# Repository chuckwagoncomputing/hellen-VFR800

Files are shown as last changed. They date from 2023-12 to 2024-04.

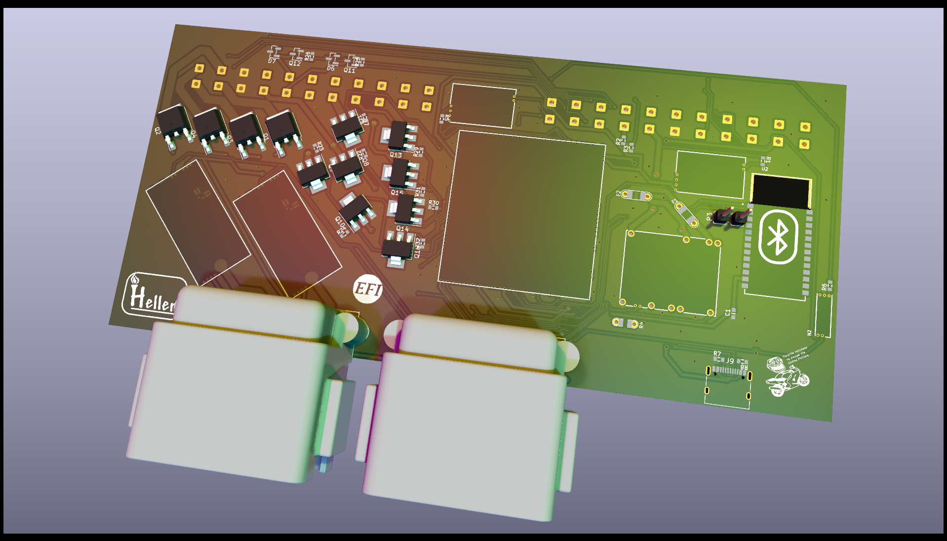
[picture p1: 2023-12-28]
uaeficopiedtovfr.png

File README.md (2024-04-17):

bumpThis repo contains files to build a standalone plug and play RusEFI Hellen based ECU for a 99 Honda VFR800. The prototype is unfinished and currently none of these files can be used to make a functioning ECU

A quick look at the wiring diagrams suggest this hardware should also be compatible with the CBR600F4i, CBR929RR, and 01-03 CBR1100xx  if the ECU connectors were repinned.

In addition to the above it may be able to replace the ignition module/ECU of a 98-08 VT1100C, 01-07 VT750DC, 02-04 VTX1800, RC51, and 2003-09 VTX1300 with some harness repinning

Features in progress as of v0.03:

Drop in ECU replacement for 99-01 VFR800 with addition of 2 wideband oxygen sensors

4x sequential ignition/injection

CANBUS

2x Wideband oxygen sensor channels

3x lowside driver output on rear connector

Inputs for analog sensor on rear connector

USB support

Bluetooth connectivity

MicroSD card for logging

VSS input to ECU for eventual implementation of traction control

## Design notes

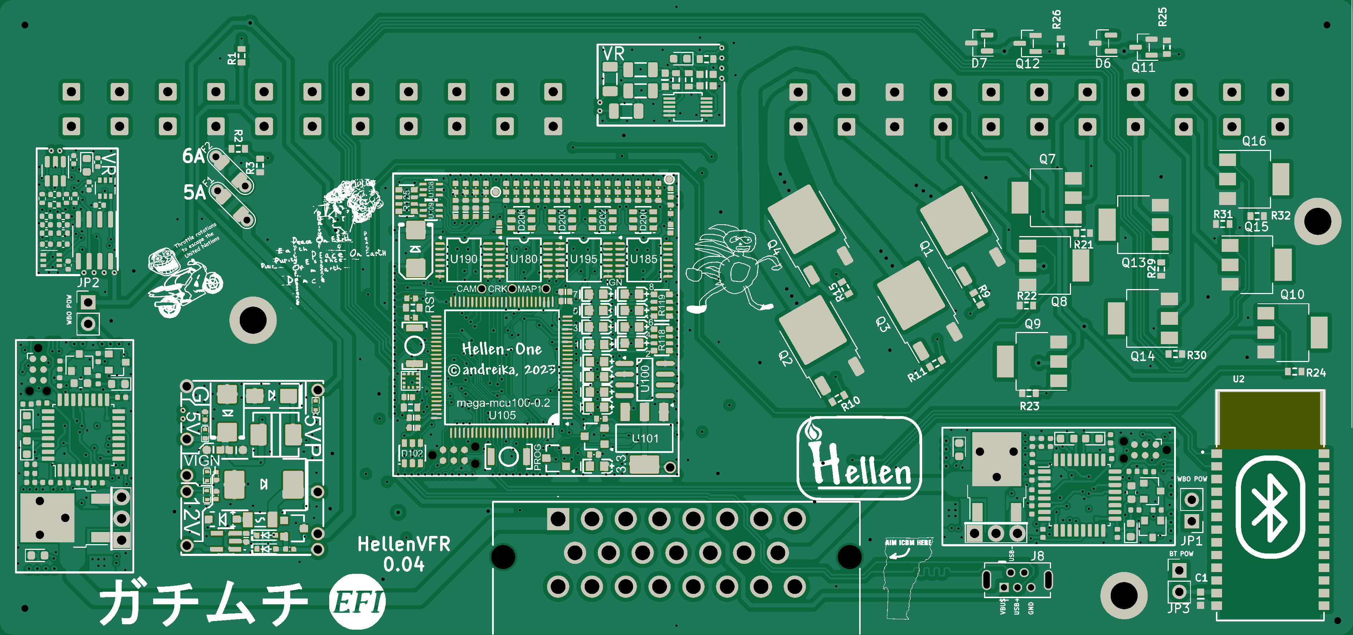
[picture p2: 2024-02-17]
boards/uaeficopiedtovfr-0.04/board/misc/uaeficopiedtovfr-0.04-top.png

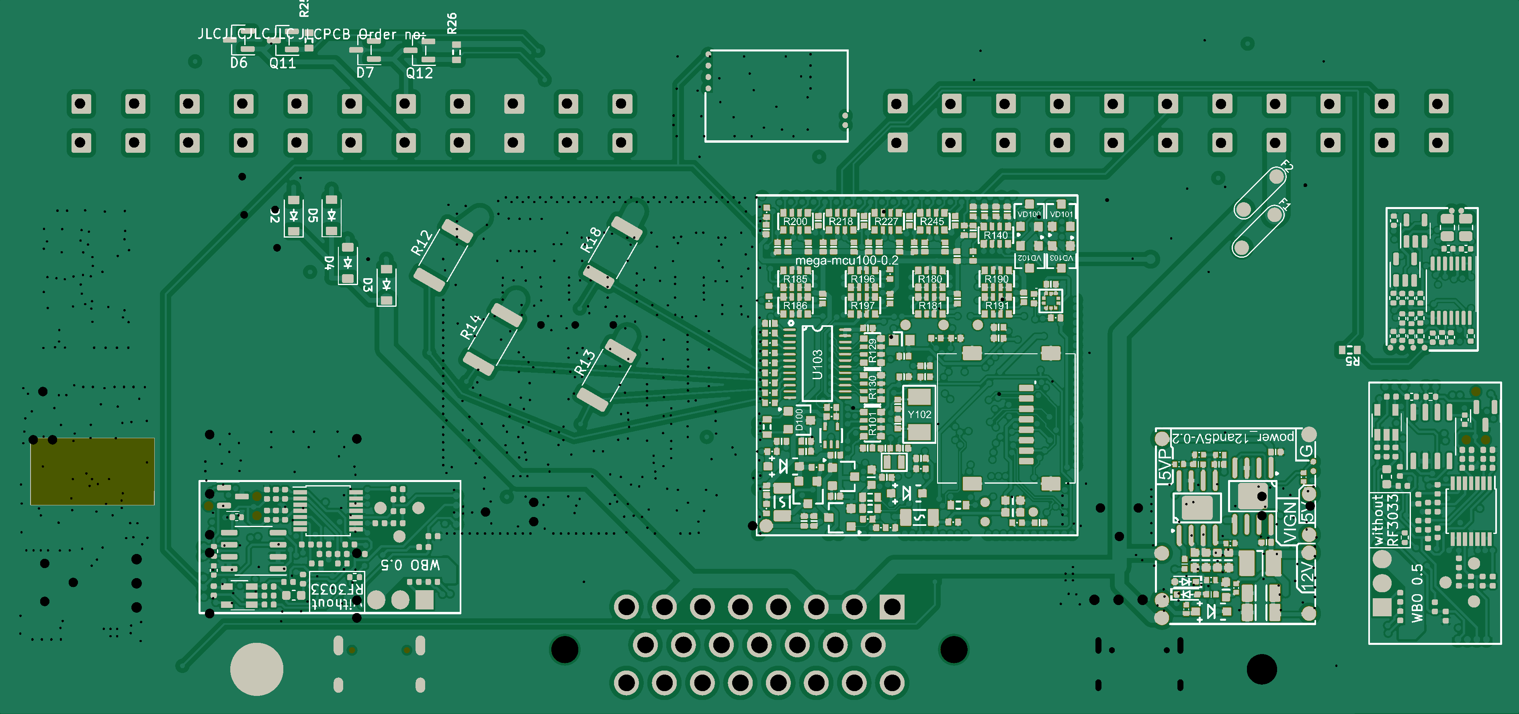
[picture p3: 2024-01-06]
boards/uaeficopiedtovfr-0.03/board/misc/uaeficopiedtovfr-0.03-bottom.png

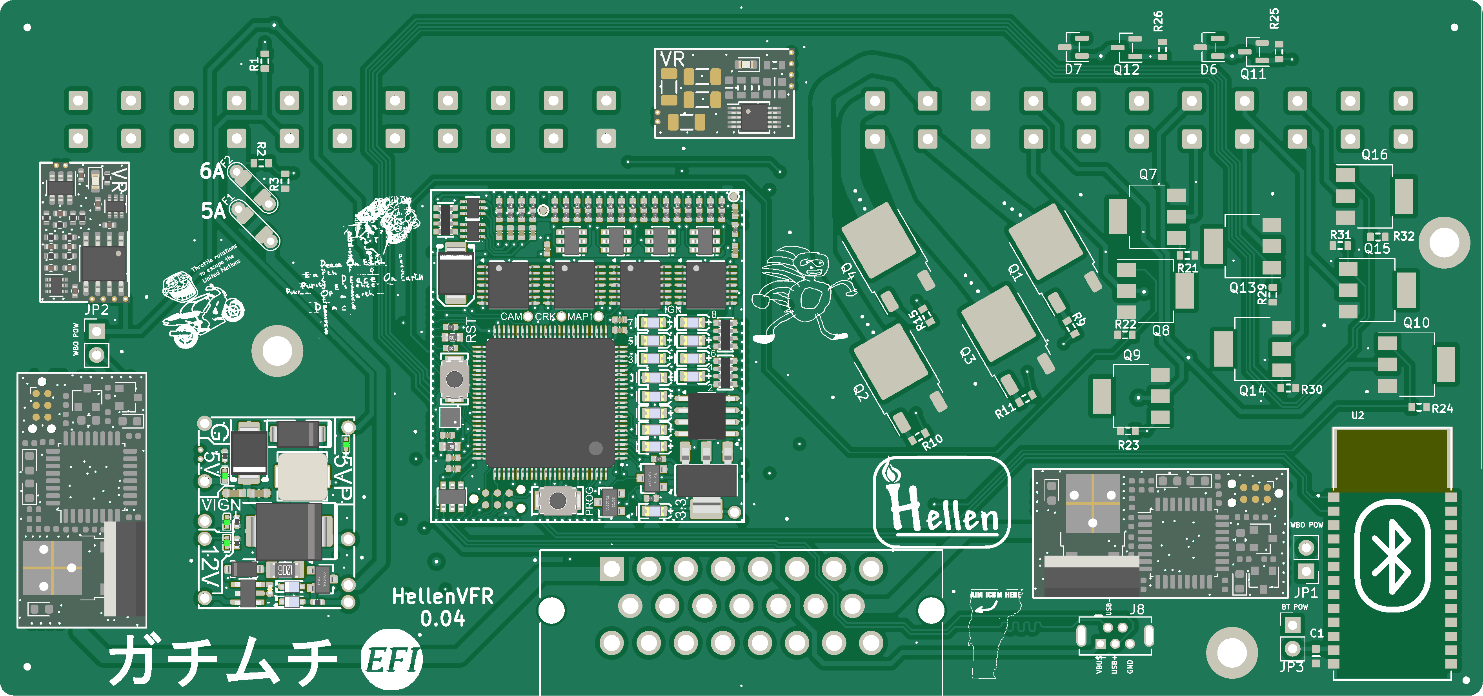
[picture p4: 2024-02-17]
boards/uaeficopiedtovfr-0.04/board/uaeficopiedtovfr-0.04.png

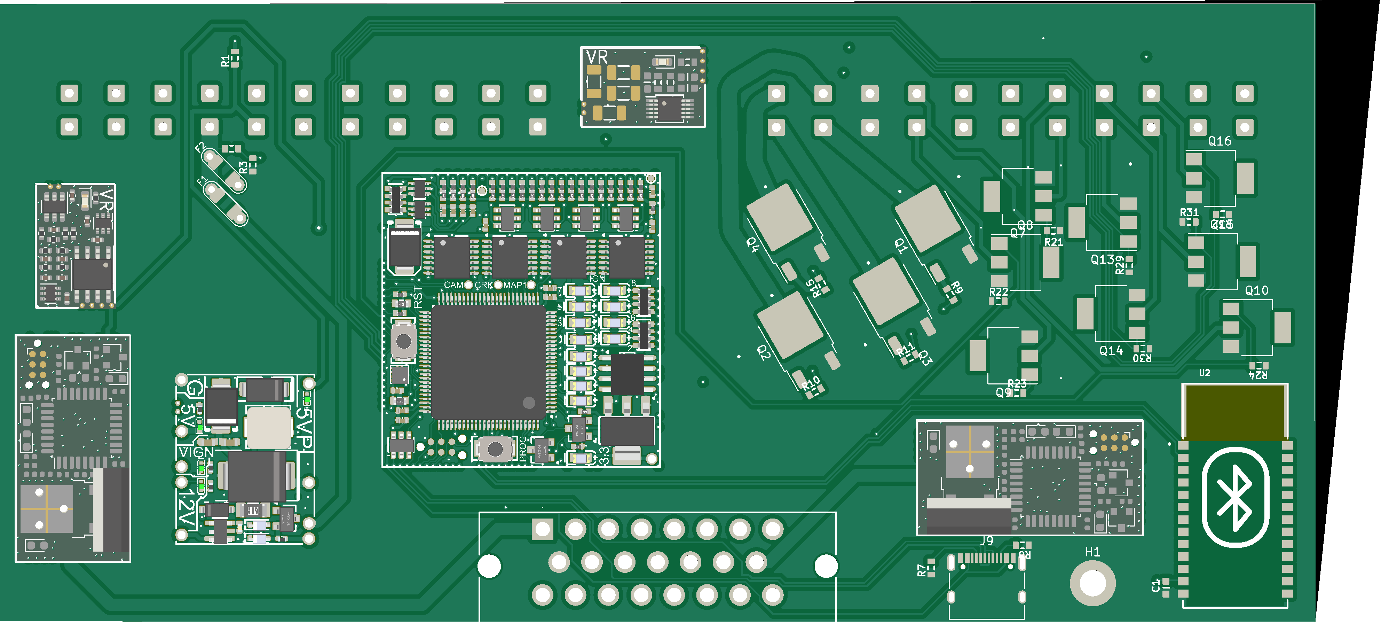
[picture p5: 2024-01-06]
boards/uaeficopiedtovfr-0.03/board/uaeficopiedtovfr-0.03.png

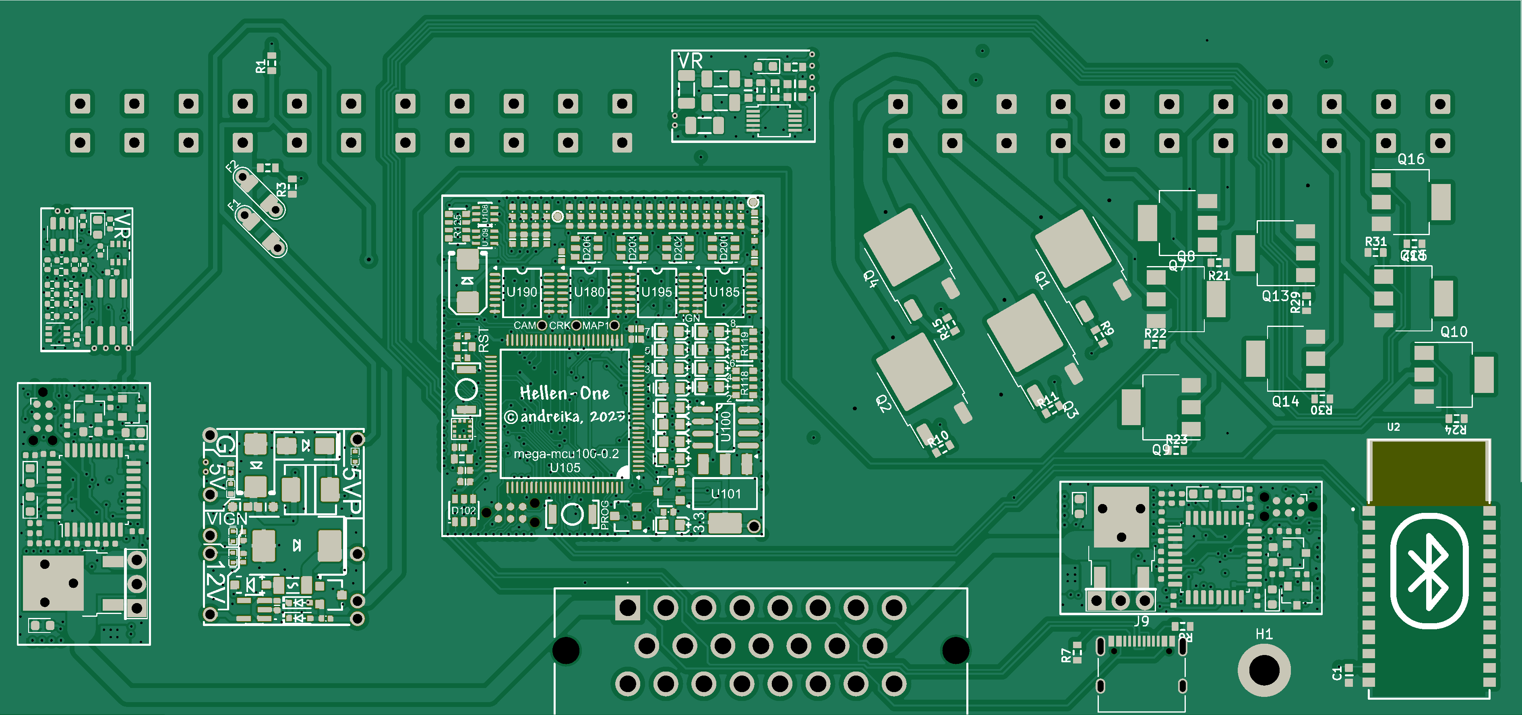
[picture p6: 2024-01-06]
boards/uaeficopiedtovfr-0.03/board/misc/uaeficopiedtovfr-0.03-top.png

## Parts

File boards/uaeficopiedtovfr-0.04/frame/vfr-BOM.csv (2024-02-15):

Comment | Designator | Footprint | LCSC Part #
100n | C1 | C0603 | C14663
B5819W | D2 | SOD-123 | C8598
B5819W | D3 | SOD-123 | C8598
B5819W | D4 | SOD-123 | C8598
B5819W | D5 | SOD-123 | C8598
PSM712-LF | D6 | SOT-23 | C32677
PSM712-LF | D7 | SOT-23 | C32677
12H1500D | F1 | PAD-1206-PAD | C182446
12H1500D | F2 | PAD-1206-PAD | C182446
RUSEFI_LOGO | G3 | rusefi_logo
LOGO | G4 | LOGO
MountingHole_Pad | H1 | MountingHole_3.2mm_M3_DIN965_Pad
MountingHole_Pad | H2 | MountingHole_3.2mm_M3_DIN965_Pad
Conn_01x06 | J3 | PinHeader_1x06_P2.54mm_Vertical | C37208
1-776087-1 | J4 | 17760871
Conn_01x06 | J6 | PinHeader_1x06_P2.54mm_Vertical | C37208
MUSBD111M0 | J7 | CONN4_BD111M0_AMP
USB_B_Mini | J8 | USB-MINI-B-VERTICAL
USB_C_Receptacle_USB2.0 | J9 | USB_C_Receptacle_XKB_U262-16XN-4BVC11 | C2927038
Jumper_2_Bridged | JP1 | PinHeader_1x02_P2.54mm_Vertical
Jumper_2_Bridged | JP2 | PinHeader_1x02_P2.54mm_Vertical
Jumper_2_Bridged | JP3 | PinHeader_1x02_P2.54mm_Vertical
Module:power_12and5V/0.2 | M1 | power_12and5V
Module:knock/0.2 | M2 | knock
Module:vr-discrete/0.4 | M3 | vr-discrete
Module:vr-max9924/0.1 | M4 | vr-max9924
Module:wbo/0.5 | M5 | wbo
Module:mega-mcu100/0.2 | M6 | mega-mcu100
Module:wbo/0.5 | M7 | wbo
Pad | P1 | PAD-TH
Pad | P2 | PAD-TH
Pad | P3 | PAD-TH
Pad | P4 | PAD-TH
ISL9V3040D3S | Q1 | DPAK
ISL9V3040D3S | Q2 | DPAK
ISL9V3040D3S | Q3 | DPAK
ISL9V3040D3S | Q4 | DPAK
ZXMS6005SGTA | Q7 | SOT-223 | C174042
ZXMS6005SGTA | Q8 | SOT-223 | C174042
ZXMS6005SGTA | Q9 | SOT-223 | C174042
ZXMS6005SGTA | Q10 | SOT-223 | C174042
AO3400A | Q11 | SOT-23 | C20917
AO3400A | Q12 | SOT-23 | C20917
ZXMS6005SGTA | Q13 | SOT-223 | C174042
ZXMS6005SGTA | Q14 | SOT-223 | C174042
ZXMS6005SGTA | Q15 | SOT-223 | C174042
ZXMS6005SGTA | Q16 | SOT-223 | C174042
4.7k | R1 | R0603
33k | R2 | R0603 | C4216
6.8k | R3 | R0603 | C23212
Jumper-Pad-Pad | R4 | PAD-0805-PAD | C17477
0 | R5 | R0603
0 | R6 | R0603 | C21189
5.6k | R7 | R0603 | C23189
5.6k | R8 | R0603 | C23189
22 | R9 | R0603 | C23345
22 | R10 | R0603 | C23345
22 | R11 | R0603 | C23345
0 | R12 | R2512 | C25469
0 | R13 | R2512 | C25469
0 | R14 | R2512 | C25469
22 | R15 | R0603 | C23345
0 | R18 | R2512 | C25469
4.7k | R21 | R0603 | C23162
4.7k | R22 | R0603 | C23162
4.7k | R23 | R0603 | C23162
4.7k | R24 | R0603 | C23162
4.7k | R25 | R0603 | C23162
4.7k | R26 | R0603 | C23162
4.7k | R29 | R0603 | C23162
4.7k | R30 | R0603 | C23162
4.7k | R31 | R0603 | C23162
4.7k | R32 | R0603 | C23162
~ | text1 | trollfaceVFR
~ | U1 | VFRboardempty
JDY-33 | U2 | JDY-33

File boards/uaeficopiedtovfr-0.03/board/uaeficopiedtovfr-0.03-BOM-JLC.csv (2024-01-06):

Comment | Designator | Footprint | LCSC Part #
100n | C1, C772 | C0603 | C14663
B5819W | D2, D3, D4, D5, D416, D417, D101, D107 | SOD-123 | C8598
PSM712-LF | D6, D7, D411 | SOT-23 | C32677
12H1500D | F1, F2 | PAD-1206-PAD | C182446
Conn_01x06 | J3, J6 | PinHeader_1x06_P2.54mm_Vertical | C37208
USB_C_Receptacle_USB2.0 | J9 | USB_C_Receptacle_XKB_U262-16XN-4BVC11 | C2927038
ZXMS6005SGTA | Q7, Q8, Q9, Q10, Q13, Q14, Q15, Q16 | SOT-223 | C174042
AO3400A | Q11, Q12, Q101, Q103 | SOT-23 | C20917
33k | R2, R120 | R0603 | C4216
6.8k | R3 | R0603 | C23212
Jumper-Pad-Pad | R4 | PAD-0805-PAD | C17477
0 | R6 | R0603 | C21189
5.6k | R7, R8 | R0603 | C23189
22 | R9, R10, R11, R15 | R0603 | C23345
0 | R12, R13, R14, R18 | R2512 | C25469
4.7k | R21, R22, R23, R24, R25, R26, R29, R30, R31, R32 | R0603 | C23162
47u | C410, C412 | C1206 | C96123
100n | C411, C413, C420 | C0402 | C307331
1u | C414, C415, C755, C758, C761, C762, C763, C765, C766, C767, C600, C607, C609, C610, C611, C600_2, C607_2, C609_2, C610_2, C611_2 | C0402 | C52923
10u | C421, C422, C423, C424, C425, C426 | C0603 | C96446
4.7u | C427, C616, C616_2 | C0603 | C19666
10n | C428, C756, C757, C760, C764, C768, C769, C202, C208, C209, C210, C211, C212, C213, C214, C215 | C0402 | C15195
220p | C429 | C0402 | C1530
1N4148WS | D410, D412, D413, D414 | SOD-323 | C2128
SMCJ30A | D418 | SMC | C310046
SS34 | D420 | SMA | C8678
P6SMB6.8CA | D421, D205 | SMB | C78395
SMD1206P050TF/24 | F410 | SMD1206 | C209741
2.2uH | L420 | L1210 | C36828
MWSA0503-10uH | L421 | MWSA0503 | C139506
MHT136UGCT | LED1, LED2, LED3, LED4 | LED0402 | C434447
6.8k | R410, R413 | R0402 | C25917
33k | R411, R424, R425 | R0402 | C25779
1 | R420 | R0402 | C25086
10k | R421, R426, R427, R757, R762, R763, R767, R768, R604, R605, R613, R614, R618, R619, R625, R102, R103, R105, R107, R108, R109, R121, R124, R126, R127, R128, R132, R135, R136, R137, R138, R139, R141, R142, R228, R229, R230, R231, R232, R233, R234, R235, R246, R247, R248, R249, R250, R251, R252, R253, R604_2, R605_2, R613_2, R614_2, R618_2, R619_2, R625_2 | R0402 | C25744
68k | R422, R760, R602, R603, R602_2, R603_2 | R0402 | C36871
12k | R423, R754 | R0402 | C25752
4.7k | R428, R144, R203, R204, R207, R208, R219, R220, R223, R224 | R0402 | C25900
MIC5205-3.3YM5 | U410 | SOT23-5 | C37970
TLS115 | U411 | PG-DSO-8 EP | C540242
LMR14020 | U420 | SOP8 | C187824
1n | C751, C135, C139, C141, C142, C143, C144, C145, C146, C200, C201, C203, C225, C226, C227, C228 | C0402 | C1523
470n | C752 | C0402 | C47339
100n | C753, C754, C759, C601, C602, C605, C608, C612, C613, C614, C615, C617, C618, C100, C101, C105, C108, C111, C112, C113, C119, C120, C122, C124, C126, C127, C130, C134, C147, C180, C185, C190, C195, C220, C221, C222, C601_2, C602_2, C605_2, C608_2, C612_2, C613_2, C614_2, C615_2, C617_2, C618_2 | C0402 | C1525
LED-GREEN-0603 | D751, D771, D601, D104, D108, D601_2 | LED-0603 | C72043
2.2k | R751, R122, R123, R146, R147 | R0402 | C25879
10k | R752, R753 | R0805 | C17414
100k | R755, R756, R758, R759, R615, R621, R615_2, R621_2 | R0402 | C25741
10 | R761, R764, R769, R606, R110, R111, R112, R113, R114, R115, R116, R117, R606_2 | R0402 | C25077
1k | R765, R766, R600, R601, R616, R617, R622, R626, R627, R628, R600_2, R601_2, R616_2, R617_2, R622_2, R626_2, R627_2, R628_2 | R0402 | C11702
SRV05-4-P-T7 | U751, D102, D200, D202, D203, D206 | SOT23-6 | C85364
74AHC1G02 | U752, U757 | SOT23-5 | C7463
MCP6004 | U753, U600, U180, U185, U190, U195, U600_2 | TSSOP14 | C50282
MAX9142 | U754 | SO8 | C18567
NC7SB3157P6X | U755, U756 | SOT-363 | C87403
1n | C771 | C0603 | C1588
22u | C773, C117, C123 | C0603 | C59461
4.7k | R771, R772, R773, R774 | R1206 | C17936
10k | R776, R777 | R0603 | C25804
MAX9924UAUB+ | U771 | MSOP-10_3x3mm_P0.5mm | C143633
33n | C603, C603_2 | C0402 | C1585
LED-RED-0603 | D600, D603, D103, D600_2, D603_2 | LED-0603 | C2286
LED-BLUE-0603 | D602, D105, D109, D110, D111, D112, D113, D114, D115, D116, D602_2 | LED-0603 | C72041
PESD1CAN | D604, D100, D604_2 | SOT-23 | C343993
VND7NV04TR-E | Q600, Q600_2 | DPAK | C155605
22k | R607, R607_2 | R0402 | C25768
47 | R608, R608_2 | R0402 | C25118
61.9 | R609, R609_2 | R0603 | C23092
20k | R610, R611, R612, R610_2, R611_2, R612_2 | R0402 | C25765
27k | R620, R623, R620_2, R623_2 | R0402 | C25771
3.3k | R624, R624_2 | R0402 | C25890
AD8628 | U601, U601_2 | TSOT23-5 | C29309
STM32F042K6Tx | U602, U602_2 | LQFP32 | C69216
REF3033 | U603, U102, U603_2 | SOT-23 | C36658
XC6206P332MR | U604, U604_2 | SOT-23 | C5446
TJA1051T/3/1J | U605, U100, U605_2 | SO-8_3.9x4.9mm_P1.27mm | C38695
STM32F429VGT6 | U105 | LQFP100 | C95448
SN74LVC4245APWR | U103 | TSSOP24 | C7859
SN74LVC1G06DCKR | U110 | SOT-353 | C7828
SMD1206B035TF/16 | F100, F101 | R1206 | C269114
Molex MicroSD 47219-2001 | J100 | SDAMB-012 | C164170
LPS22HBTR | U107 | HLGA-10L | C94049
LIS2DH12TR | U106 | LGA12 | C110926
LED-YELLOW-0603 | D106 | LED-0603 | C72038
LDL1117S33R | U101 | SOT-223 | C435835
BTN | S100, S101 | SMD-2_2.9x3.9x1.7 | C115357
BLM18AG601SN1D | L100 | L0603 | C19330
BAT54S | VD100, VD101, VD102, VD103 | SOT-23 | C47546
AO3401A | Q100, Q102 | SOT-23 | C15127
680k | R201, R202, R205, R206, R221, R222, R225, R226 | R0402 | C163456
510 | R133, R134 | R0603 | C23193
510 | R254, R255, R256, R258 | R0402 | C25123
470 | R101, R118, R119 | R0603-4 | C25510
120 | R100 | R0603 | C22787
100 | R104, R106 | R0603 | C22775
74LVC2G17GW,125 | U108, U109 | SOT-363 | C80500
32.768 kHz | Y101 | SMD2012 | C99009
20 MHz | Y102 | SMD5032 | C112566
18p | C132, C136 | C0402 | C1549
12p | C115, C116 | C0402 | C1547
10k | R129, R130, R140 | R0603-4 | C29718
5.1k | R195 | R0402 | C25905
4.7u | C102, C103, C104, C106, C107, C137, C138, C140 | C0402 | C23733
4.7k | R125, R180, R181, R185, R186, R190, R191, R196, R197, R200, R218, R227, R245 | R0603-4 | C66697
2.2u | C114, C131, C223, C224, C229 | C0402 | C12530
1u | C133 | C0603 | C519560
0 | R131, R143, R145, R148 | R0402 | C17168
nSMD050-24V | F42333310 | SMD1206 | C70076

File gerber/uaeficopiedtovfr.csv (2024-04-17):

Comment | Designator | Footprint | LCSC Part #
100n | C1 | hellen-one-common:C0603 | C14663
B5819W | D2 | hellen-one-common:SOD-123 | C8598
B5819W | D3 | hellen-one-common:SOD-123 | C8598
B5819W | D4 | hellen-one-common:SOD-123 | C8598
B5819W | D5 | hellen-one-common:SOD-123 | C8598
PSM712-LF | D6 | hellen-one-common:SOT-23 | C32677
PSM712-LF | D7 | hellen-one-common:SOT-23 | C32677
12H1500D | F1 | hellen-one-common:PAD-1206-PAD | C182446
12H1500D | F2 | hellen-one-common:PAD-1206-PAD | C182446
RUSEFI_LOGO | G3 | kicad6-libraries:rusefi_logo
LOGO | G4 | hellen-one-common:LOGO
MountingHole_Pad | H1 | MountingHole:MountingHole_3.2mm_M3_DIN965_Pad
MountingHole_Pad | H2 | MountingHole:MountingHole_3.2mm_M3_DIN965_Pad
Conn_01x06 | J3 | Connector_PinHeader_2.54mm:PinHeader_1x06_P2.54mm_Vertical | C37208
1-776087-1 | J4 | 17760871
Conn_01x06 | J6 | Connector_PinHeader_2.54mm:PinHeader_1x06_P2.54mm_Vertical | C37208
MUSBD111M0 | J7 | usbb:CONN4_BD111M0_AMP
USB_B_Mini | J8 | hellen-one-common:USB-MINI-B-VERTICAL
USB_C_Receptacle_USB2.0 | J9 | Connector_USB:USB_C_Receptacle_XKB_U262-16XN-4BVC11 | C2927038
Jumper_2_Bridged | JP1 | Connector_PinHeader_2.54mm:PinHeader_1x02_P2.54mm_Vertical
Jumper_2_Bridged | JP2 | Connector_PinHeader_2.54mm:PinHeader_1x02_P2.54mm_Vertical
Jumper_2_Bridged | JP3 | Connector_PinHeader_2.54mm:PinHeader_1x02_P2.54mm_Vertical
Module-power_12and5V-0.2 | M1 | hellen-one-power_12and5V-0.2:power_12and5V
Module-knock-0.2 | M2 | hellen-one-knock-0.2:knock
Module-vr-discrete-0.4 | M3 | hellen-one-vr-discrete-0.4:vr-discrete
Module-vr-max9924-0.1 | M4 | hellen-one-vr-max9924-0.1:vr-max9924
Module-wbo-0.5 | M5 | hellen-one-wbo-0.5:wbo
Module:mega-mcu100/0.2 | M6 | hellen-one-mega-mcu100-0.2:mega-mcu100
Module-wbo-0.5 | M7 | hellen-one-wbo-0.5:wbo
Pad | P1 | hellen-one-common:PAD-TH
Pad | P2 | hellen-one-common:PAD-TH
Pad | P3 | hellen-one-common:PAD-TH
Pad | P4 | hellen-one-common:PAD-TH
ISL9V3040D3S | Q1 | Package_TO_SOT_SMD:TO-252-2
ISL9V3040D3S | Q2 | Package_TO_SOT_SMD:TO-252-2
ISL9V3040D3S | Q3 | Package_TO_SOT_SMD:TO-252-2
ISL9V3040D3S | Q4 | Package_TO_SOT_SMD:TO-252-2
ZXMS6005SGTA | Q7 | Package_TO_SOT_SMD:SOT-223 | C174042
ZXMS6005SGTA | Q8 | Package_TO_SOT_SMD:SOT-223 | C174042
ZXMS6005SGTA | Q9 | Package_TO_SOT_SMD:SOT-223 | C174042
ZXMS6005SGTA | Q10 | Package_TO_SOT_SMD:SOT-223 | C174042
AO3400A | Q11 | hellen-one-common:SOT-23 | C20917
AO3400A | Q12 | hellen-one-common:SOT-23 | C20917
ZXMS6005SGTA | Q13 | Package_TO_SOT_SMD:SOT-223 | C174042
ZXMS6005SGTA | Q14 | Package_TO_SOT_SMD:SOT-223 | C174042
ZXMS6005SGTA | Q15 | Package_TO_SOT_SMD:SOT-223 | C174042
ZXMS6005SGTA | Q16 | Package_TO_SOT_SMD:SOT-223 | C174042
4.7k | R1 | hellen-one-common:R0603
33k | R2 | hellen-one-common:R0603 | C4216
6.8k | R3 | hellen-one-common:R0603 | C23212
Jumper-Pad-Pad | R4 | hellen-one-common:PAD-0805-PAD | C17477
0 | R5 | hellen-one-common:R0603
0 | R6 | hellen-one-common:R0603 | C21189
5.6k | R7 | hellen-one-common:R0603 | C23189
5.6k | R8 | hellen-one-common:R0603 | C23189
22 | R9 | hellen-one-common:R0603 | C23345
22 | R10 | hellen-one-common:R0603 | C23345
22 | R11 | hellen-one-common:R0603 | C23345
0 | R12 | Resistor_SMD:R_2512_6332Metric | C25469
0 | R13 | Resistor_SMD:R_2512_6332Metric | C25469
0 | R14 | Resistor_SMD:R_2512_6332Metric | C25469
22 | R15 | hellen-one-common:R0603 | C23345
470k | R16 | hellen-one-common:R0603 | C23162
0 | R18 | Resistor_SMD:R_2512_6332Metric | C25469
4.7k | R21 | hellen-one-common:R0603 | C23162
4.7k | R22 | hellen-one-common:R0603 | C23162
4.7k | R23 | hellen-one-common:R0603 | C23162
4.7k | R24 | hellen-one-common:R0603 | C23162
4.7k | R25 | hellen-one-common:R0603 | C23162
4.7k | R26 | hellen-one-common:R0603 | C23162
4.7k | R29 | hellen-one-common:R0603 | C23162
4.7k | R30 | hellen-one-common:R0603 | C23162
4.7k | R31 | hellen-one-common:R0603 | C23162
4.7k | R32 | hellen-one-common:R0603 | C23162
~ | text1 | Customparts:trollfaceVFR
~ | U1 | Customparts:VFRboardempty
JDY-33 | U2 | kicad6-libraries:JDY-33

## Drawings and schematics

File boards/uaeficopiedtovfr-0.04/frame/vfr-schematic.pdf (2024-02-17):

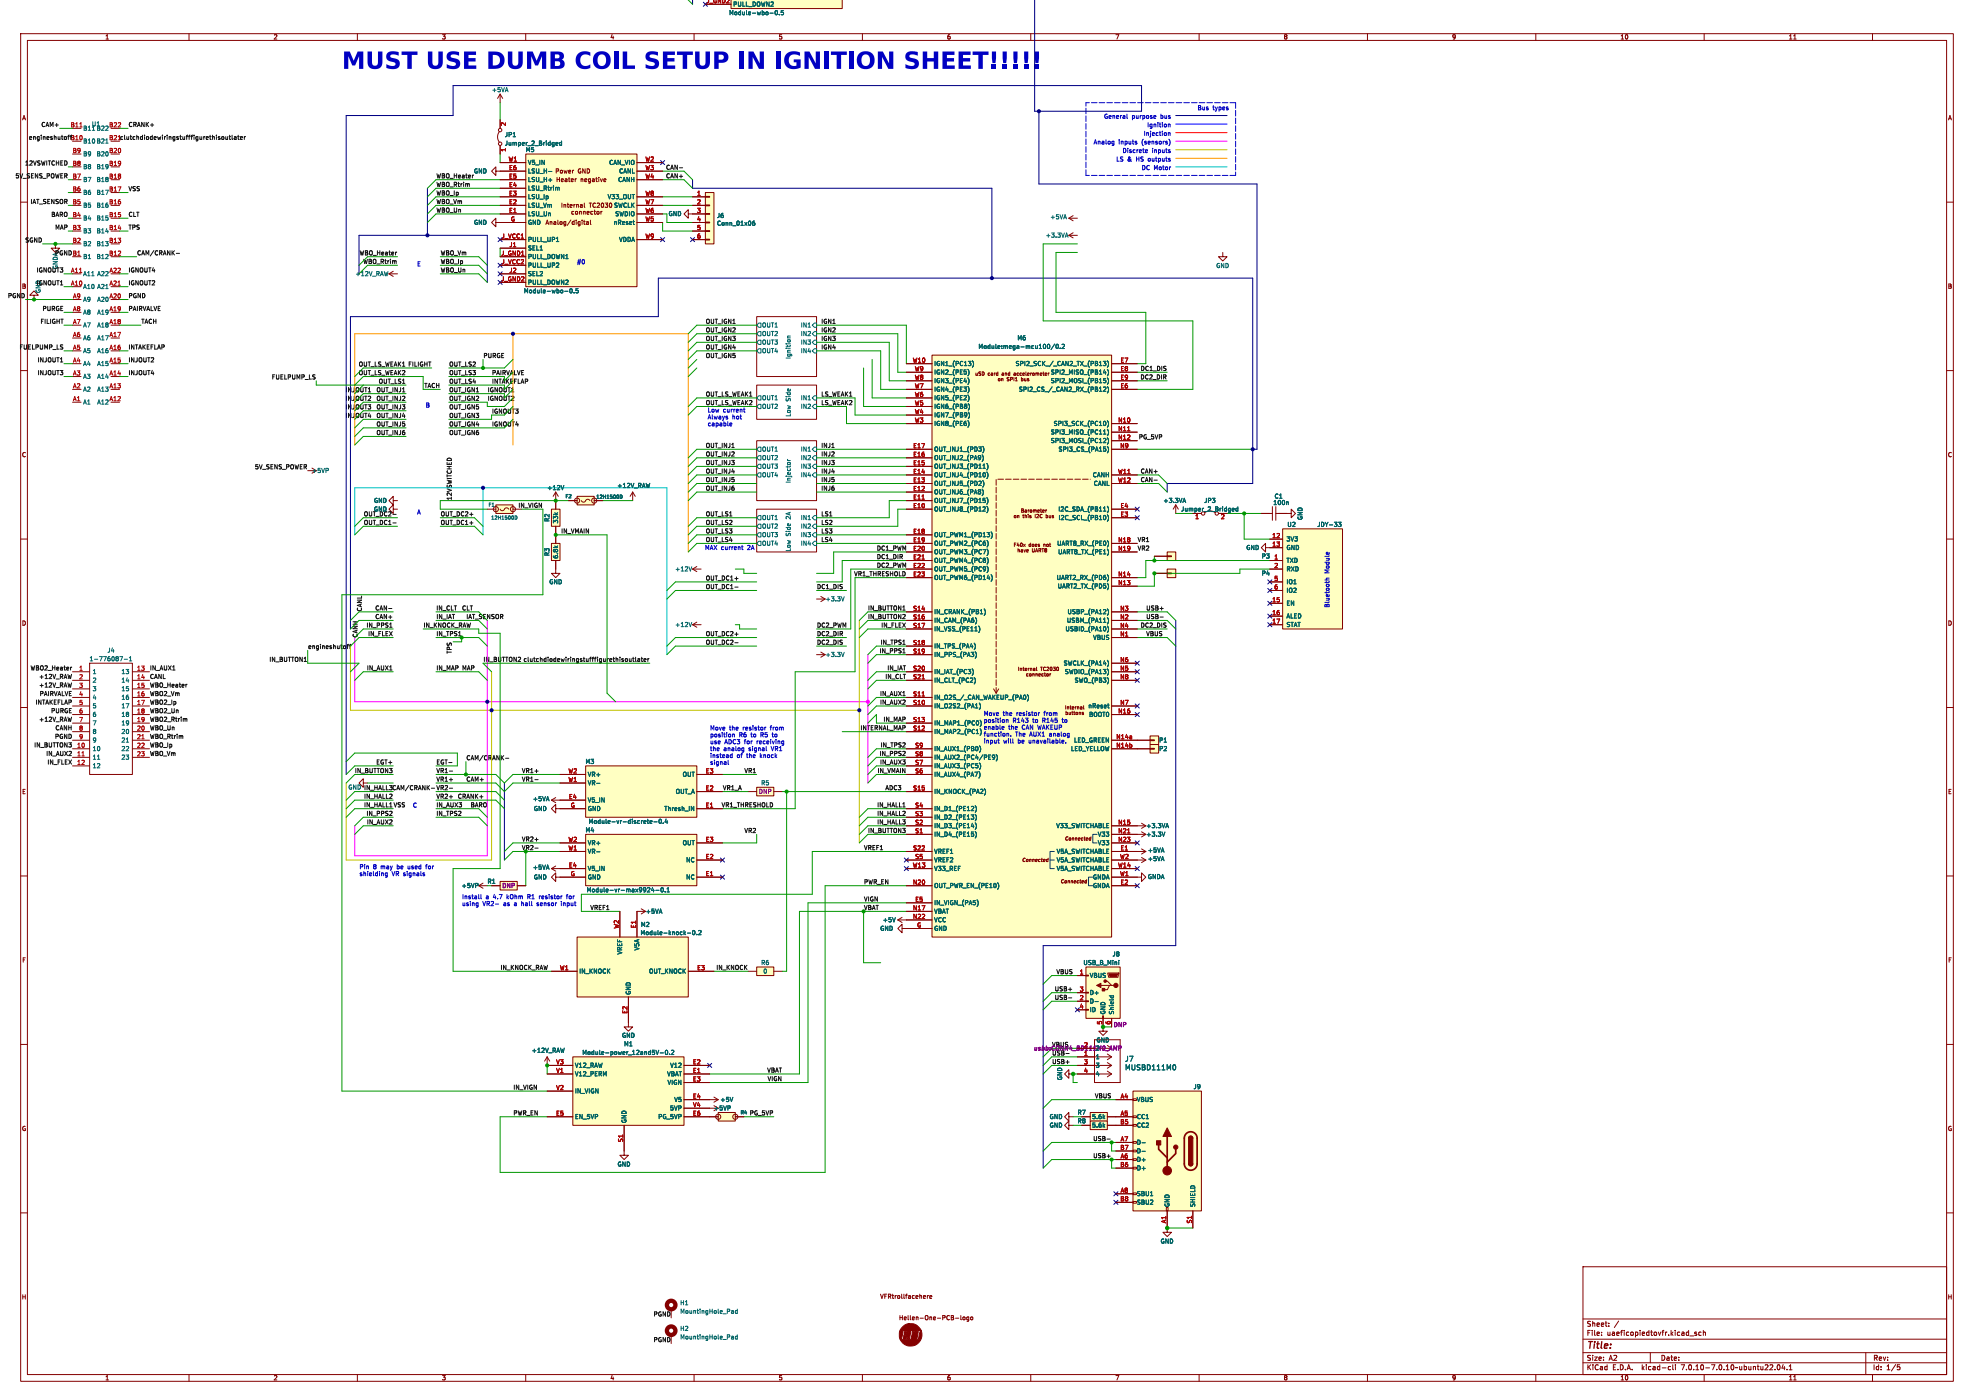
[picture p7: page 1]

#0 MUST USE DUMB COIL SETUP IN IGNITION SHEET!!!!!

CAM+
clutchdiodewiringstufffigurethisoutlater TPS CLT SGND

Analog/digital Heater negative Power GND

enable the CAN WAKEUP

use ADC3 for receiving
the analog signal VR1
instead of the knock

IN_VIGN_(PA5) E5
VBUS USB- USB+ USB- VBUS USB+ VBUS

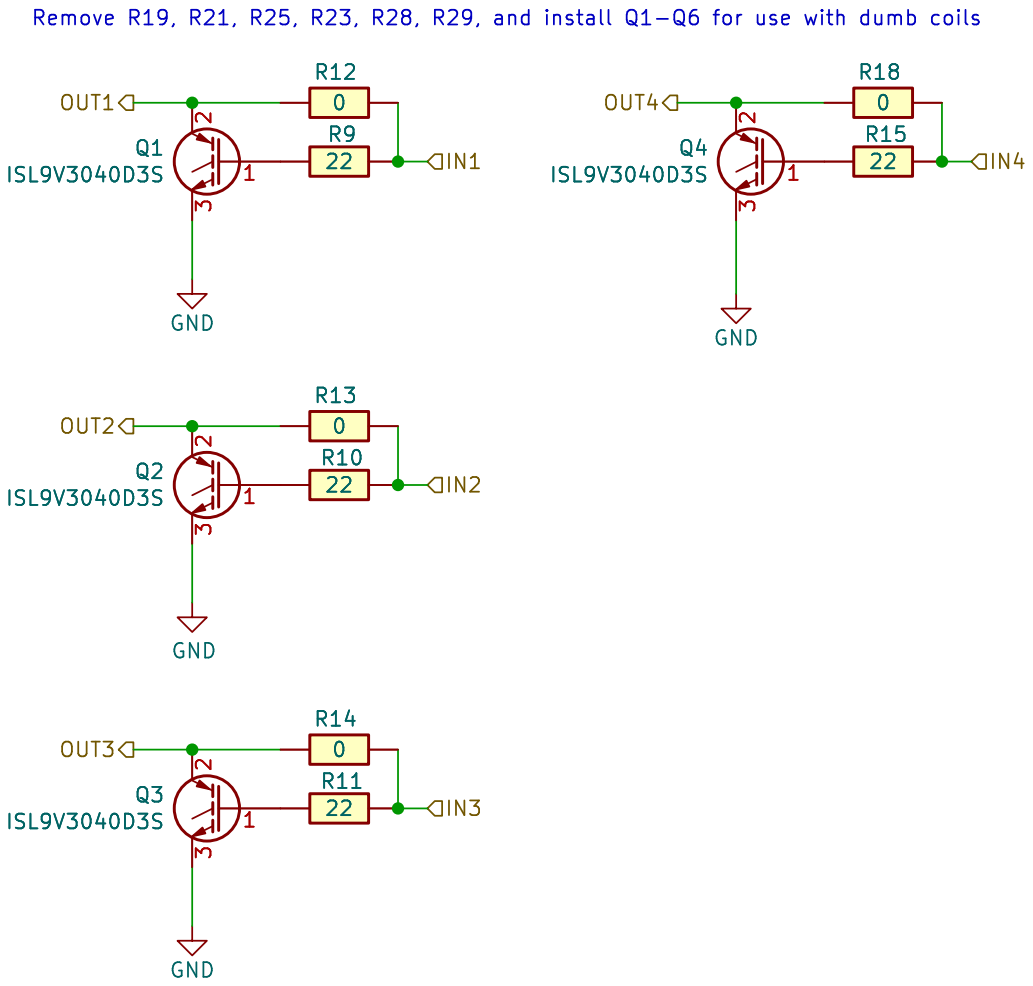
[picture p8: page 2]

File: IGN6.kicad_sch Sheet: /Ignition/ rusefi.com

Id: 2/5 Title: UAEFI Ignition

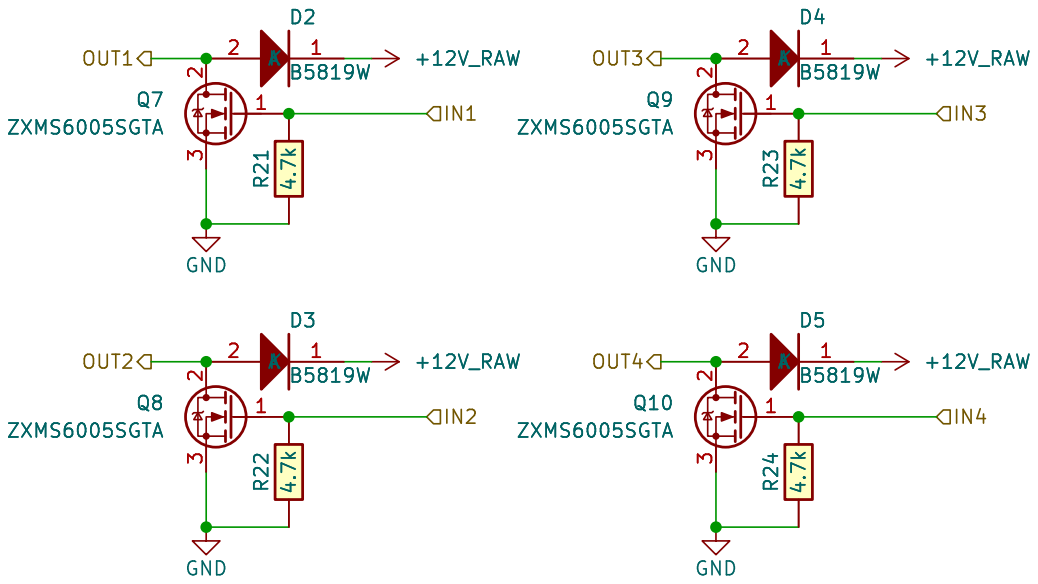
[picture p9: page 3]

File: LS4.kicad_sch Sheet: /Low Side 2A/ rusefi.com

Id: 4/5 Title: UAEFI Low Side

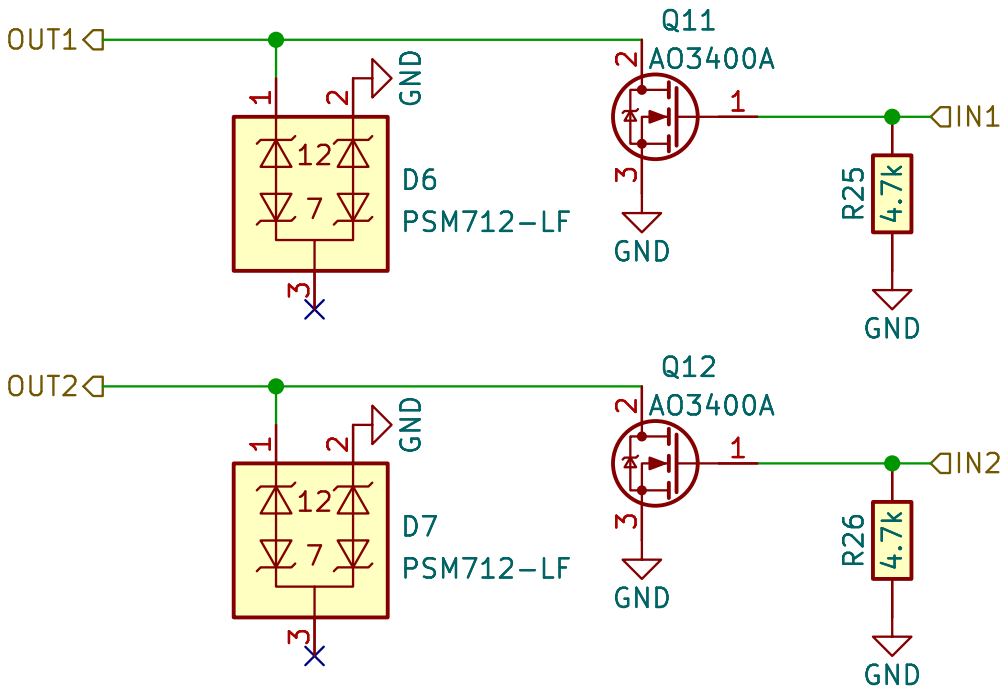
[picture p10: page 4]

Id: 5/5 Title: UAEF Low Side low current File: LS_weak.kicad_sch Sheet: /Low Side/ rusefi.com

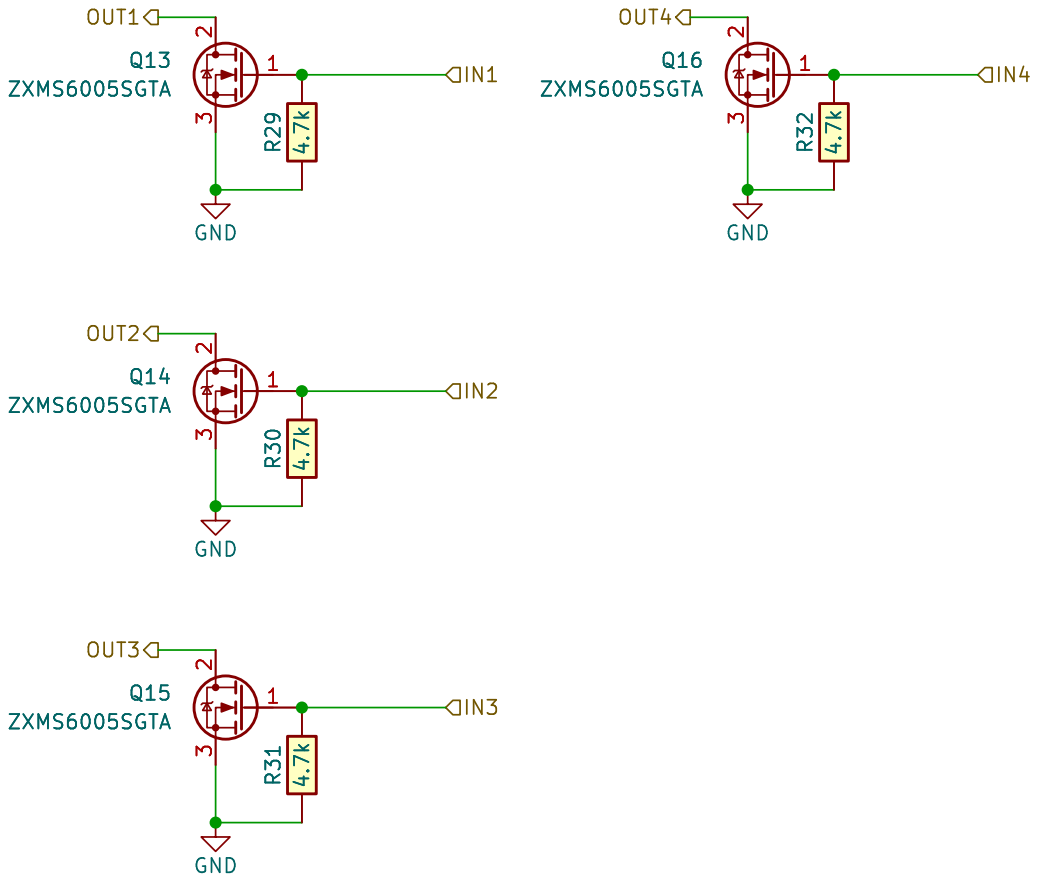
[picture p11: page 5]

Id: 9/5 Title: UAEFI Injector File: INJ6.kicad_sch Sheet: /Injector/ rusefi.com

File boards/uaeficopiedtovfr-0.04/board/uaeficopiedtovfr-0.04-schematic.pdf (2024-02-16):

# IN3 Ignition OUT3 OUT2 OUT1 IN1

# IGN4 OUT_DC2+


#0 MUST USE DUMB COIL SETUP IN IGNITION SHEET!!!!!

CAM+
clutchdiodewiringstufffigurethisoutlater TPS CLT SGND

Analog/digital Heater negative Power GND

enable the CAN WAKEUP

use ADC3 for receiving
the analog signal VR1
instead of the knock

IN_VIGN_(PA5) E5
VBUS USB- USB+ USB- VBUS USB+ VBUS


File: IGN6.kicad_sch Sheet: /Ignition/ rusefi.com

Id: 2/5 Title: UAEFI Ignition

D Date: 2023-11-01 KiCad; kicad-cli; 7.0.10-7.0.10~ubuntu22.04.1 Size: A4; Rev:; 2 3 Q10 ZXMS6005SGTA R21 4.7k 1; 2 3 Q7 ZXMS6005SGTA R22 4.7k K; +12V_RAW; GND; 2 3 Q9 ZXMS6005SGTA GND; +12V_RAW 1 A; D4B5819W R²³ 4.7k 1; 2 3 Q8 ZXMS6005SGTA GND; D5B5819W R²⁴ 4.7k; OUT3 OUT2 OUT1; OUT4; IN3 +12V_RAW; 2 R²⁴ 4.7k R²³ 4.7k; 2 Q10 ZXMS6005SGTA; 2 3 Q9 ZXMS6005SGTA; 2 3 +12V_RAW; 2 R²² 4.7k R²¹ 4.7k Q7 ZXMS6005SGTA 1; 2 Q8 ZXMS6005SGTA

File: LS4.kicad_sch Sheet: /Low Side 2A/ rusefi.com

Id: 4/5 Title: UAEFI Low Side

D Date: 2023-11-01 KiCad; kicad-cli; 7.0.10-7.0.10~ubuntu22.04.1 Size: A4; Rev:; GND; 2 3 Q11 AO3400A GND GND; 3 D6PSM712-LF GND R26 4.7k 12; IN1 OUT1 OUT2; 2 3 GND GND; D6PSM712-LF; 3 D7PSM712-LF; 2 3 GND

3 D7PSM712-LF GND GND R25 4.7k

3 GND GND R25 4.7k R26 4.7k GND Q12 AO3400A

Id: 5/5 Title: UAEF Low Side low current File: LS_weak.kicad_sch Sheet: /Low Side/ rusefi.com


Id: 9/5 Title: UAEFI Injector File: INJ6.kicad_sch Sheet: /Injector/ rusefi.com

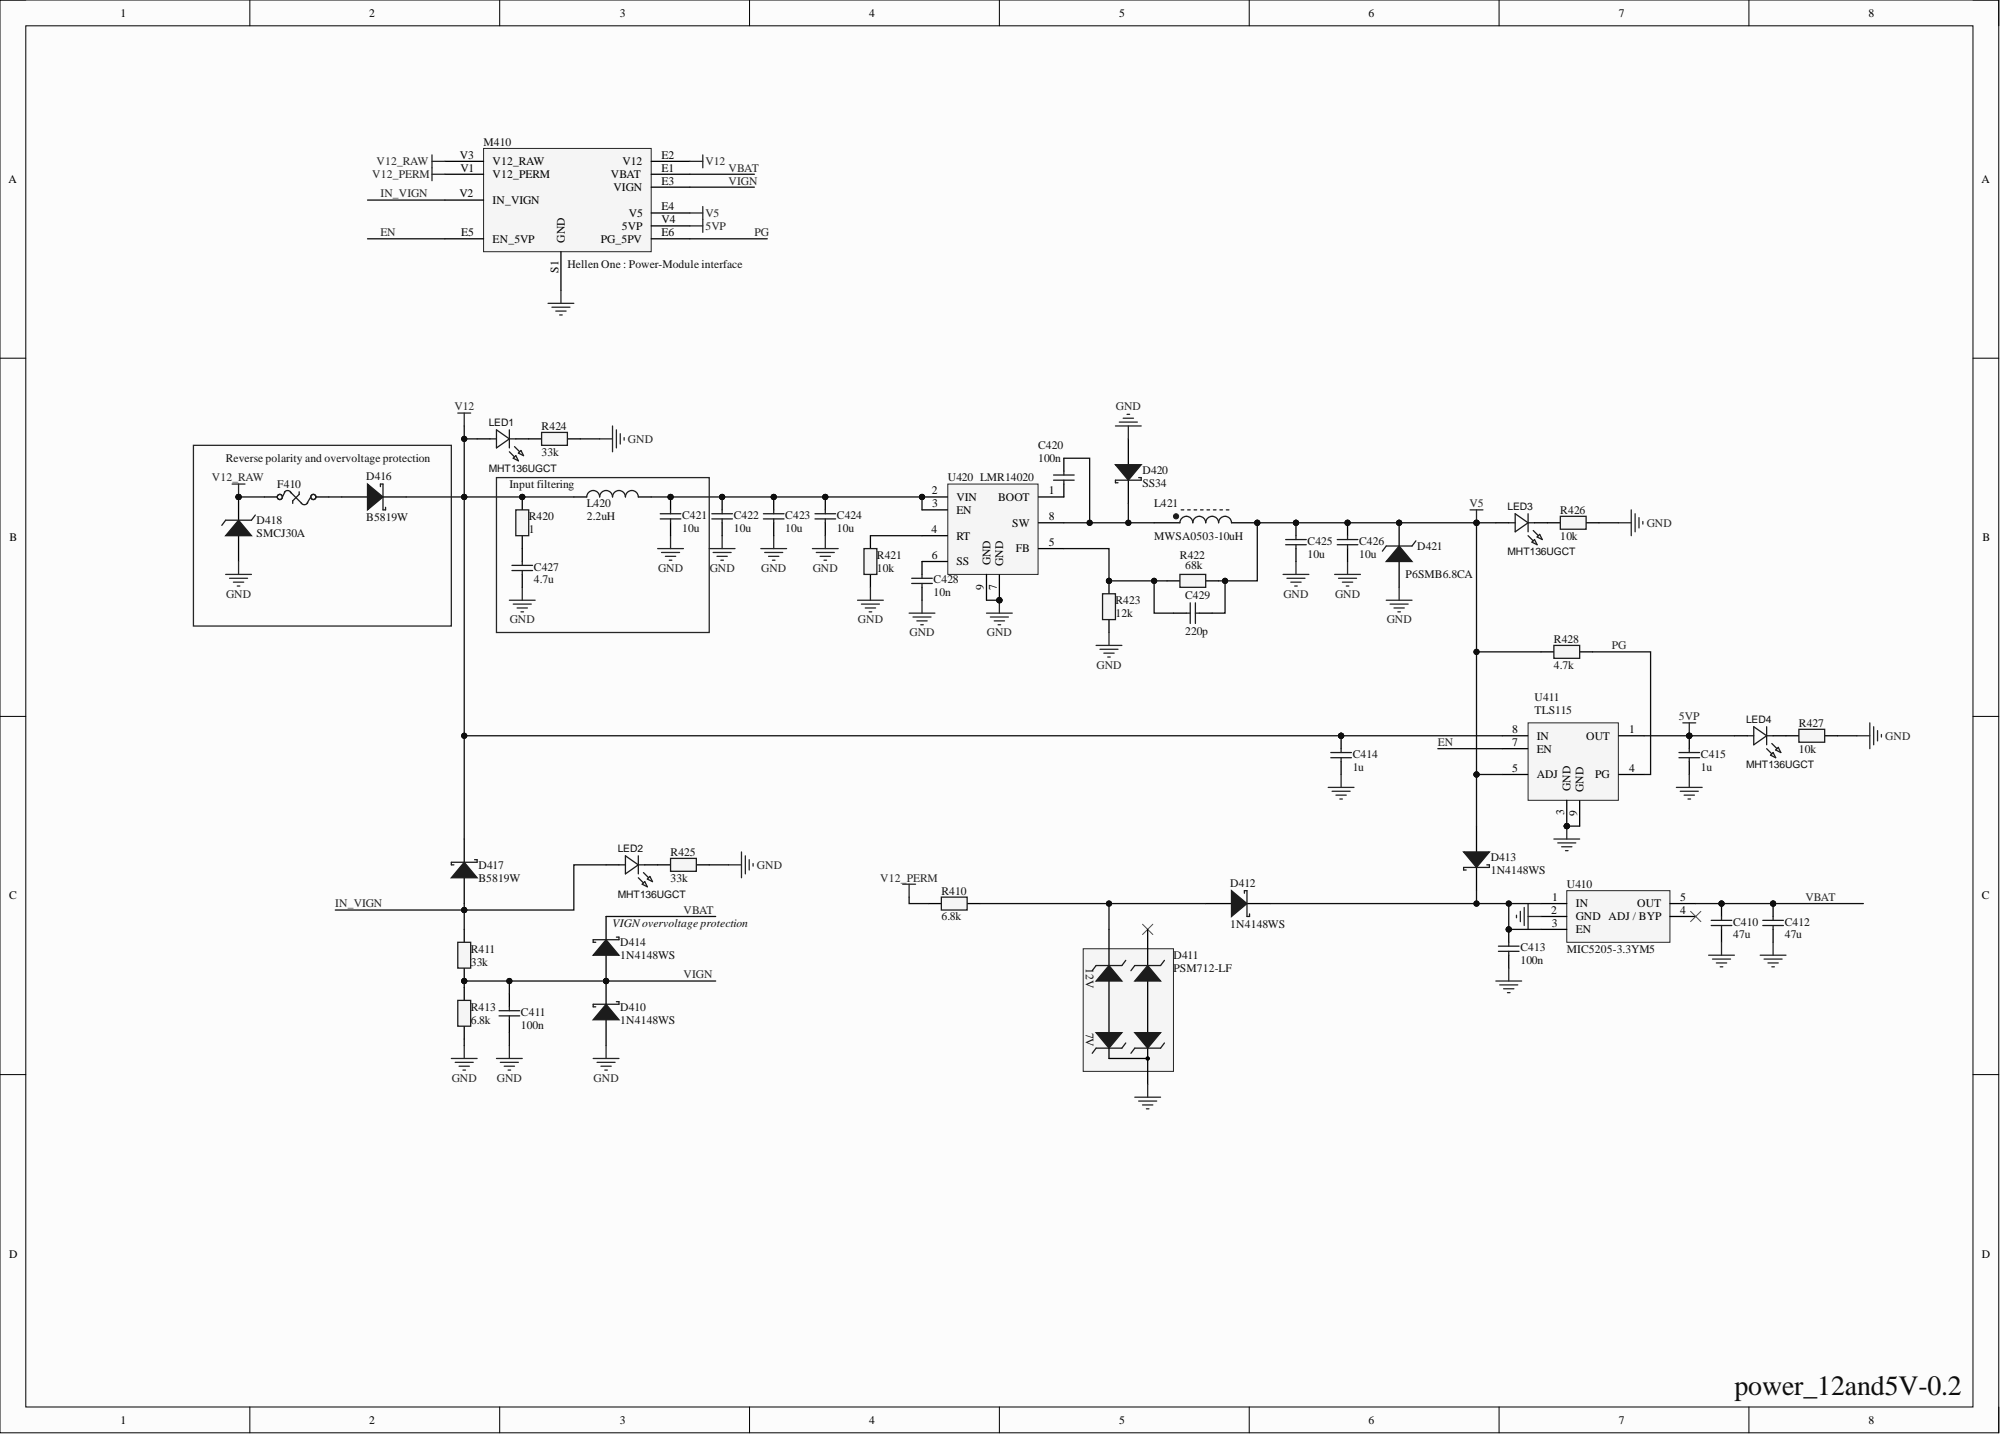
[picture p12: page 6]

Hellen One : Power-Module interface

Reverse polarity and overvoltage protection
F410 V12_RAW

## +5VGND

## +5VGND

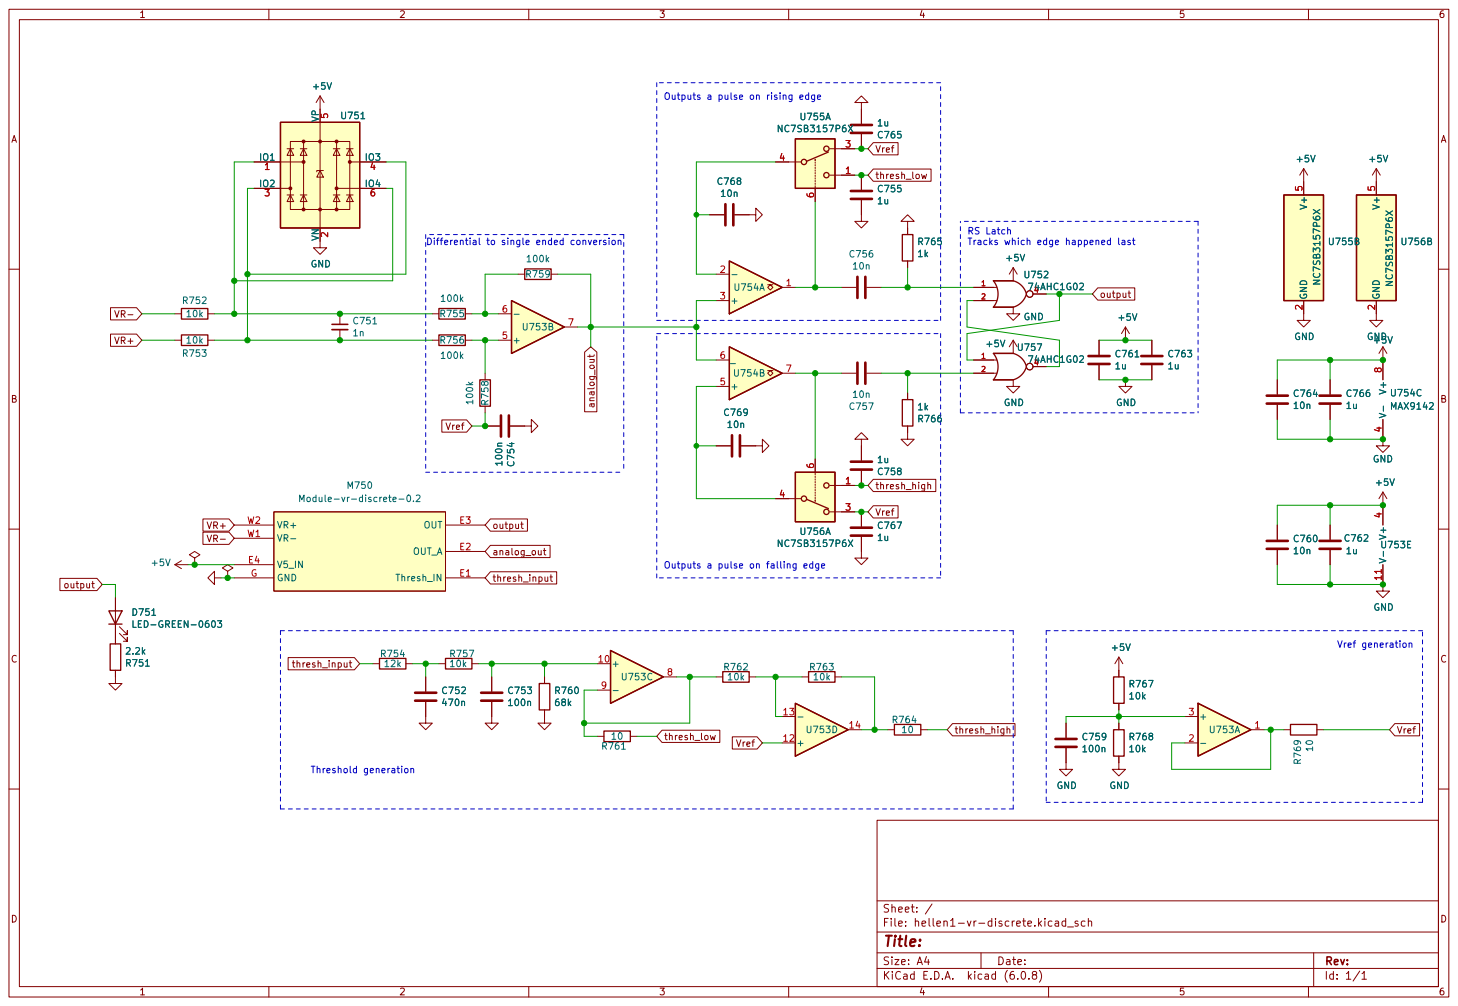
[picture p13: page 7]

Outputs a pulse on rising edge R751

Vref generation RS Latch Tracks which edge happened last
4 GND GND

Differential to single ended conversion

Outputs a pulse on falling edge

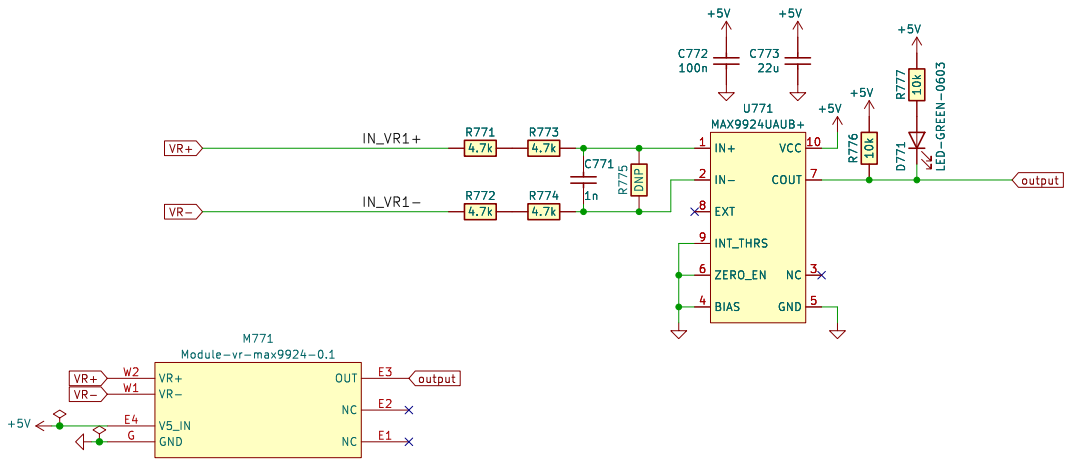
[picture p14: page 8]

Id: 1/1 Title: VR MAX9924 module

+3.3V C616

27k +

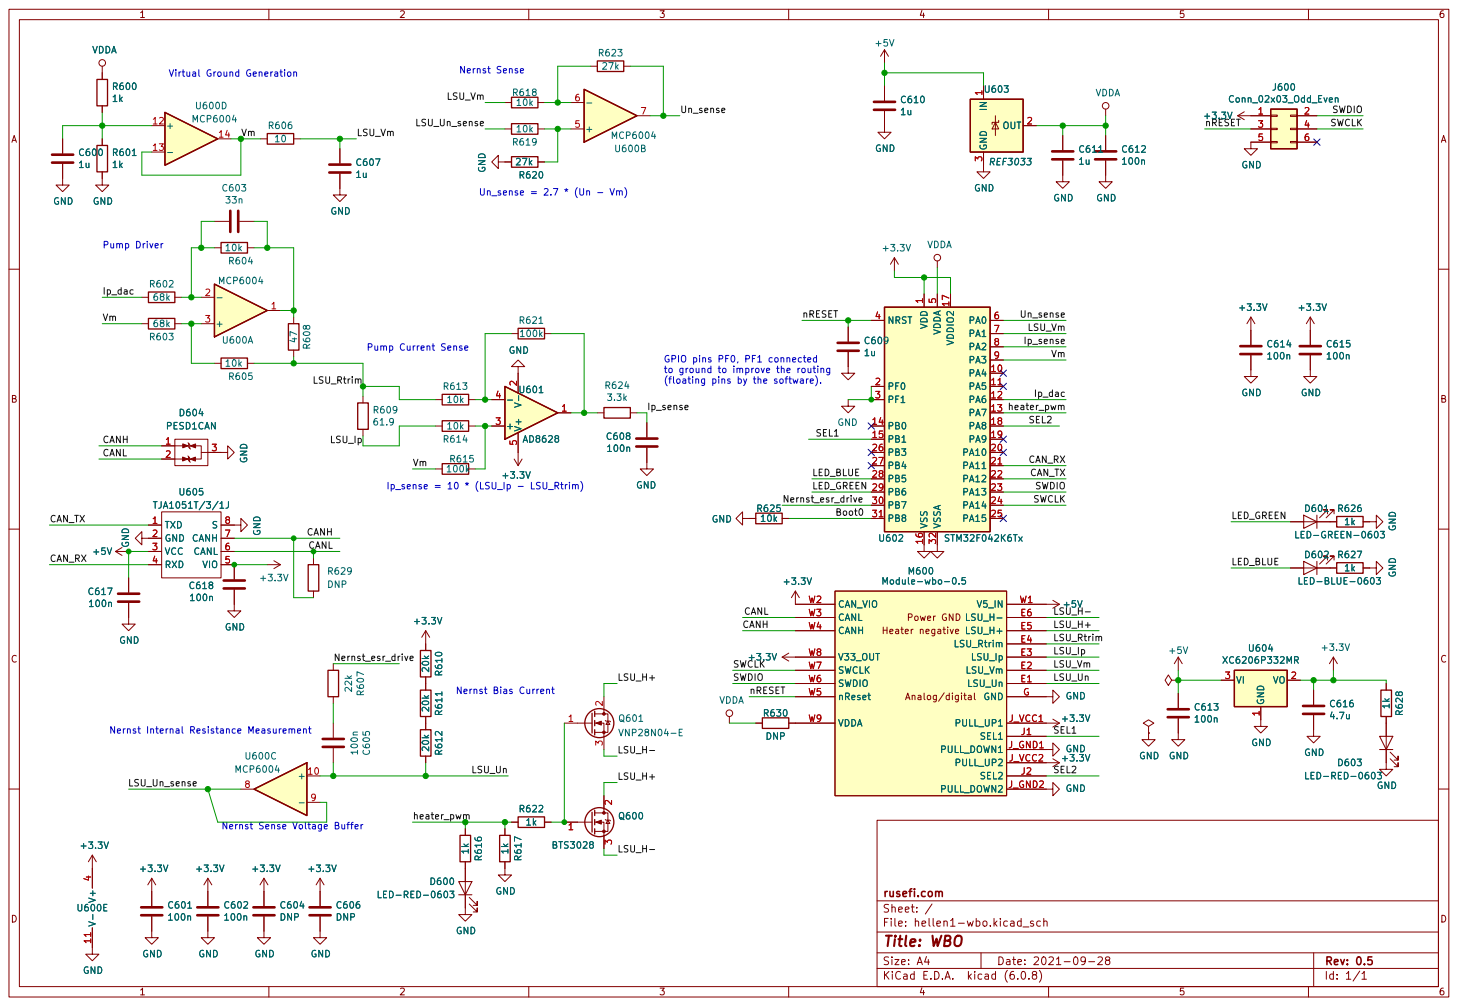
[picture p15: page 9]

100n GND GND R⁶⁰⁸ ⁴⁷

1 PA4 10 PA5 11 PA6 12 PA7 13 PB0 14 PB1 15 VSS 16 VDDIO2 17 PA8 18 PA9 19 PF0 2 PA10 20 PA11 21 PA12 22 PA13 23 PA14 24 PA15 25 PB3 26 PB4 27 PB5 28 PB6 29 PF1 3 PB7 30 PB8 31 VSSA 32 NRST 4 VDDA

1u GND GND GND
+3.3V R⁶¹¹ ²⁰k R⁶¹⁰ ²⁰k GND

to ground to improve the routing
(floating pins by the software).

Heater negative Power GND

VDDA GND
Nernst Sense Voltage Buffer Nernst Internal Resistance Measurement

+3.3V C606 DNP GND
File: hellen1-wbo.kicad_sch Sheet: / rusefi.com V⁻ 11 V⁺

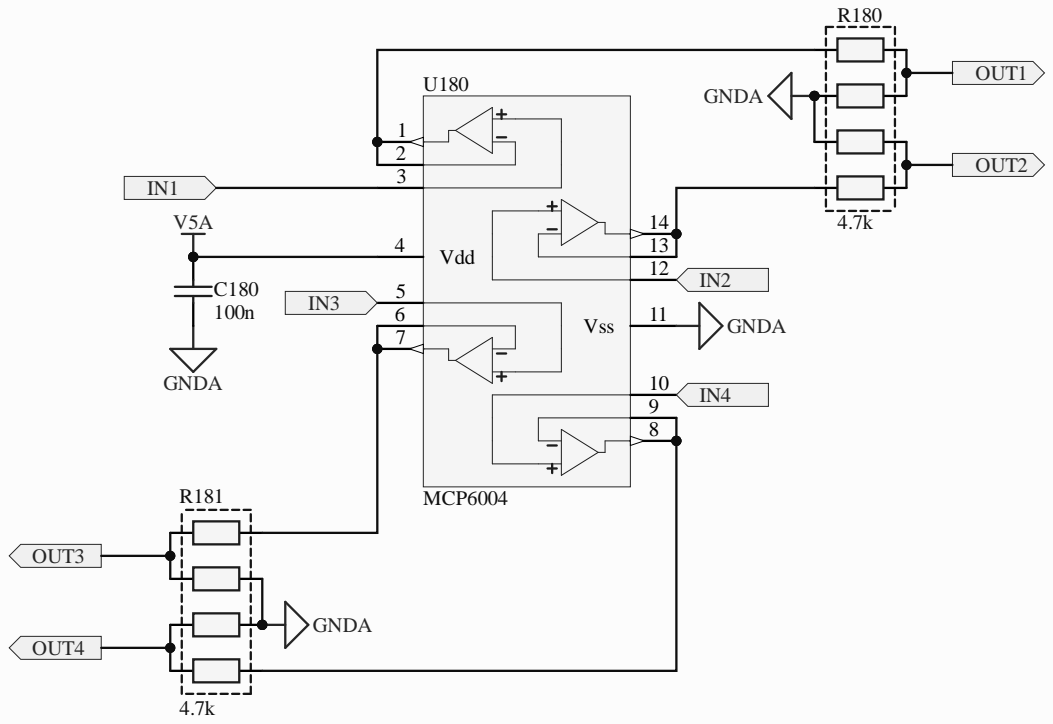
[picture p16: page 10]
Vdd 4; Vss 6; MCP6004; GNDA; OUT1; OUT2; OUT3; OUT4; C180 PIC18001 100n; PIC18002 COC3; PIR18001; PIR18002; PIR18003; PIR18004; PIR18005; PIR18006; PIR18007; PIR18008; COR5; PIR18101; PIR18102; PIR18103; PIR18105; PIR18104; PIR18106; PIR18107; PIR18108; COR6; PIU18001; PIU18002; PIU18003; PIU18004; PIU18005; PIU18006; PIU18007; PIU18008; PIU18009; PIU180010; PIU180011; PIU180012; PIU180013; PIU180014; COU2; PIC18001; POOUT2; POOUT1; POOUT3; POOUT4; POIN1; POIN3 PIU18005; PIU180010 POIN4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

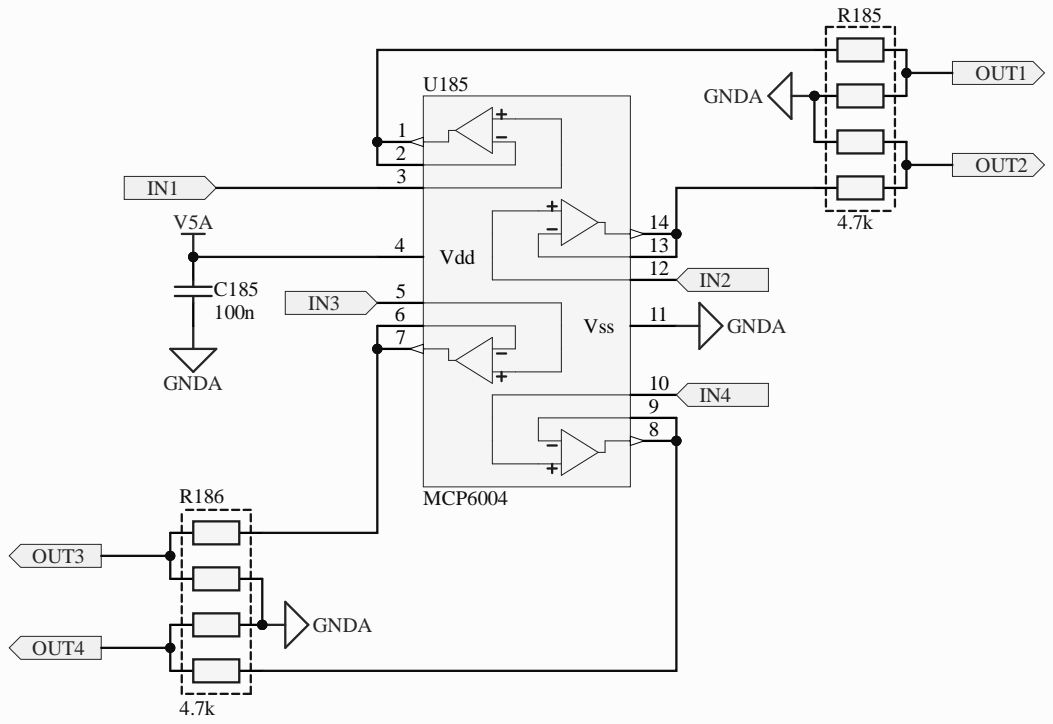
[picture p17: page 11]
Vdd 4; Vss 6; MCP6004; GNDA; OUT1; OUT2; OUT3; OUT4; C185 PIC18501 100n; PIC18502 COC3; PIR18501; PIR18502; PIR18503; PIR18504; PIR18505; PIR18506; PIR18507; PIR18508; COR5; PIR18601; PIR18602; PIR18603; PIR18605; PIR18604; PIR18606; PIR18607; PIR18608; COR6; PIU18501; PIU18502; PIU18503; PIU18504; PIU18505; PIU18506; PIU18507; PIU18508; PIU18509; PIU185010; PIU185011; PIU185012; PIU185013; PIU185014; COU2; PIC18501; POOUT2; POOUT1; POOUT3; POOUT4; POIN1; POIN3 PIU18505; PIU185010 POIN4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

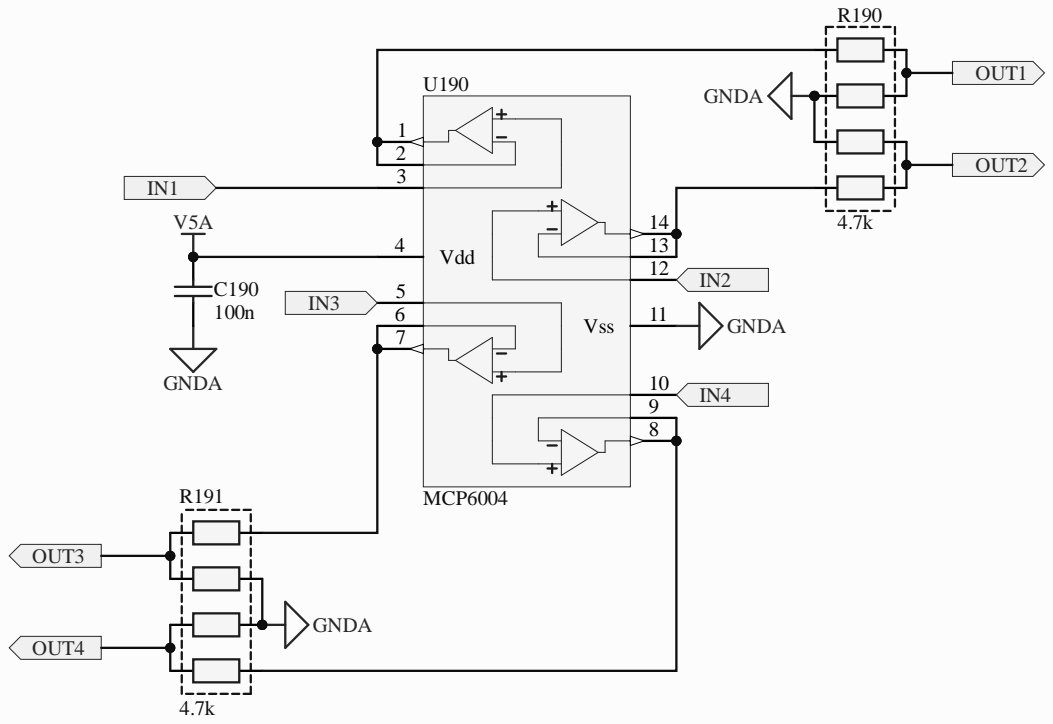
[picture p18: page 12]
Vdd 4; Vss 6; MCP6004; GNDA; OUT1; OUT2; OUT3; OUT4; C190 PIC19001 100n; PIC19002 COC3; PIR19001; PIR19002; PIR19003; PIR19004; PIR19005; PIR19006; PIR19007; PIR19008; COR5; PIR19101; PIR19102; PIR19103; PIR19105; PIR19104; PIR19106; PIR19107; PIR19108; COR6; PIU19001; PIU19002; PIU19003; PIU19004; PIU19005; PIU19006; PIU19007; PIU19008; PIU19009; PIU190010; PIU190011; PIU190012; PIU190013; PIU190014; COU2; PIC19001; POOUT2; POOUT1; POOUT3; POOUT4; POIN1; POIN3 PIU19005; PIU190010 POIN4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

SPI_; VCC; 5 SPI_SCK; 7 SPI_O; lex MicroSD; _MIS


R143 populated: analog input O2S
R145 populated: WAKEUP by CAN

*VIGN input is unprotected!
*A21 is duplicated for ADC and EINT




D100 PESD1CAN; GND; TXD 1 GND 2 VCC 3; Vio; 5 RXD 4; CANL; 6 CANH; TJA1051T/3/1J; CAN_TX; CAN_RX; VCC; CANH; CANL C100 100n
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

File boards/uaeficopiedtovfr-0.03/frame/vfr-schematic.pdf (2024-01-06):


Injection Discrete inputs General purpose bus Analog inputs (sensors) E

signal MAX current 2A MUST USE DUMB COIL SETUP IN IGNITION SHEET!!!!!

Analog/digital Heater negative Power GND

enable the CAN WAKEUP

use ADC3 for receiving
the analog signal VR1
instead of the knock

Hellen-One-PCB-logo VFRtrollfacehere


File: IGN6.kicad_sch Sheet: /Ignition/ rusefi.com

Id: 2/5 Title: UAEFI Ignition


File: LS4.kicad_sch Sheet: /Low Side 2A/ rusefi.com

Id: 4/5 Title: UAEFI Low Side

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


Id: 9/5 Title: UAEFI Injector File: INJ6.kicad_sch Sheet: /Injector/ rusefi.com

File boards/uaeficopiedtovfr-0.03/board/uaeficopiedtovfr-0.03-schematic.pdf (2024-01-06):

IN3 Ignition OUT3 OUT2 OUT1 | IN1
nReset | W5 SWDIO | W6 SWCLK | W7 V33_OUT | W8 VDDA | W9 M5 Module-wbo-0.5 | +12V


Injection Discrete inputs General purpose bus Analog inputs (sensors) E

signal MAX current 2A MUST USE DUMB COIL SETUP IN IGNITION SHEET!!!!!

Analog/digital Heater negative Power GND

enable the CAN WAKEUP

use ADC3 for receiving
the analog signal VR1
instead of the knock

Hellen-One-PCB-logo VFRtrollfacehere


File: IGN6.kicad_sch Sheet: /Ignition/ rusefi.com

Id: 2/5 Title: UAEFI Ignition

D Date: 2023-11-01 KiCad; kicad-cli; 7.0.10-7.0.10~ubuntu22.04.1 Size: A4; Rev:; 2 3 Q10 ZXMS6005SGTA R21 4.7k 1; 2 3 Q7 ZXMS6005SGTA R22 4.7k K; +12V_RAW; GND; 2 3 Q9 ZXMS6005SGTA GND; +12V_RAW 1 A; D4B5819W R²³ 4.7k 1; 2 3 Q8 ZXMS6005SGTA GND; D5B5819W R²⁴ 4.7k; OUT3 OUT2 OUT1; OUT4; IN3 +12V_RAW; 2 R²⁴ 4.7k R²³ 4.7k; 2 Q10 ZXMS6005SGTA; 2 3 Q9 ZXMS6005SGTA; 2 3 +12V_RAW; 2 R²² 4.7k R²¹ 4.7k Q7 ZXMS6005SGTA 1; 2 Q8 ZXMS6005SGTA

File: LS4.kicad_sch Sheet: /Low Side 2A/ rusefi.com

Id: 4/5 Title: UAEFI Low Side

D Date: 2023-11-01 KiCad; kicad-cli; 7.0.10-7.0.10~ubuntu22.04.1 Size: A4; Rev:; GND; 2 3 Q11 AO3400A GND GND; 3 D6PSM712-LF GND R26 4.7k 12; IN1 OUT1 OUT2; 2 3 GND GND; D6PSM712-LF; 3 D7PSM712-LF; 2 3 GND

3 D7PSM712-LF GND GND R25 4.7k

3 GND GND R25 4.7k R26 4.7k GND Q12 AO3400A

Id: 5/5 Title: UAEF Low Side low current File: LS_weak.kicad_sch Sheet: /Low Side/ rusefi.com


Id: 9/5 Title: UAEFI Injector File: INJ6.kicad_sch Sheet: /Injector/ rusefi.com


Hellen One : Power-Module interface

Reverse polarity and overvoltage protection
F410 V12_RAW

## +5VGND

## +5VGND


Outputs a pulse on rising edge R751

Vref generation RS Latch Tracks which edge happened last
4 GND GND

Differential to single ended conversion

Outputs a pulse on falling edge


Id: 1/1 Title: VR MAX9924 module

+3.3V C616

27k +


100n GND GND R⁶⁰⁸ ⁴⁷

1 PA4 10 PA5 11 PA6 12 PA7 13 PB0 14 PB1 15 VSS 16 VDDIO2 17 PA8 18 PA9 19 PF0 2 PA10 20 PA11 21 PA12 22 PA13 23 PA14 24 PA15 25 PB3 26 PB4 27 PB5 28 PB6 29 PF1 3 PB7 30 PB8 31 VSSA 32 NRST 4 VDDA

1u GND GND GND
+3.3V R⁶¹¹ ²⁰k R⁶¹⁰ ²⁰k GND

to ground to improve the routing
(floating pins by the software).

Heater negative Power GND

VDDA GND
Nernst Sense Voltage Buffer Nernst Internal Resistance Measurement

+3.3V C606 DNP GND
File: hellen1-wbo.kicad_sch Sheet: / rusefi.com V⁻ 11 V⁺

Vdd 4; Vss 6; MCP6004; GNDA; OUT1; OUT2; OUT3; OUT4; C180 PIC18001 100n; PIC18002 COC3; PIR18001; PIR18002; PIR18003; PIR18004; PIR18005; PIR18006; PIR18007; PIR18008; COR5; PIR18101; PIR18102; PIR18103; PIR18105; PIR18104; PIR18106; PIR18107; PIR18108; COR6; PIU18001; PIU18002; PIU18003; PIU18004; PIU18005; PIU18006; PIU18007; PIU18008; PIU18009; PIU180010; PIU180011; PIU180012; PIU180013; PIU180014; COU2; PIC18001; POOUT2; POOUT1; POOUT3; POOUT4; POIN1; POIN3 PIU18005; PIU180010 POIN4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

Vdd 4; Vss 6; MCP6004; GNDA; OUT1; OUT2; OUT3; OUT4; C185 PIC18501 100n; PIC18502 COC3; PIR18501; PIR18502; PIR18503; PIR18504; PIR18505; PIR18506; PIR18507; PIR18508; COR5; PIR18601; PIR18602; PIR18603; PIR18605; PIR18604; PIR18606; PIR18607; PIR18608; COR6; PIU18501; PIU18502; PIU18503; PIU18504; PIU18505; PIU18506; PIU18507; PIU18508; PIU18509; PIU185010; PIU185011; PIU185012; PIU185013; PIU185014; COU2; PIC18501; POOUT2; POOUT1; POOUT3; POOUT4; POIN1; POIN3 PIU18505; PIU185010 POIN4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

Vdd 4; Vss 6; MCP6004; GNDA; OUT1; OUT2; OUT3; OUT4; C190 PIC19001 100n; PIC19002 COC3; PIR19001; PIR19002; PIR19003; PIR19004; PIR19005; PIR19006; PIR19007; PIR19008; COR5; PIR19101; PIR19102; PIR19103; PIR19105; PIR19104; PIR19106; PIR19107; PIR19108; COR6; PIU19001; PIU19002; PIU19003; PIU19004; PIU19005; PIU19006; PIU19007; PIU19008; PIU19009; PIU190010; PIU190011; PIU190012; PIU190013; PIU190014; COU2; PIC19001; POOUT2; POOUT1; POOUT3; POOUT4; POIN1; POIN3 PIU19005; PIU190010 POIN4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

SPI_; VCC; 5 SPI_SCK; 7 SPI_O; lex MicroSD; _MIS


R143 populated: analog input O2S
R145 populated: WAKEUP by CAN

*VIGN input is unprotected!
*A21 is duplicated for ADC and EINT



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

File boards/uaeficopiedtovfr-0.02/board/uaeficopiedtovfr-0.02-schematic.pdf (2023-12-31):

# IN3 Ignition OUT3 OUT2 OUT1 IN1

+3.3VA 123456


Injection DC Motor LS & HS outputs Discrete inputs

Analog/digital Heater negative Power GND

enable the CAN WAKEUP
input will be unavailable.

use ADC3 for receiving
the analog signal VR1
instead of the knock

Hellen-One-PCB-logo


File: IGN6.kicad_sch Sheet: /Ignition/ rusefi.com

Id: 2/5 Title: UAEFI Ignition

D Date: 2023-11-01 KiCad; kicad-cli; 7.0.9-7.0.9~ubuntu22.04.1 Size: A4; Rev:; 2 3 Q10 ZXMS6005SGTA R21 4.7k 1; 2 3 Q7 ZXMS6005SGTA R22 4.7k K; +12V_RAW; GND; 2 3 Q9 ZXMS6005SGTA GND; +12V_RAW 1 A; D4B5819W R²³ 4.7k 1; 2 3 Q8 ZXMS6005SGTA GND; D5B5819W R²⁴ 4.7k; OUT3 OUT2 OUT1; OUT4; IN3 +12V_RAW; 2 R²⁴ 4.7k R²³ 4.7k; 2 Q10 ZXMS6005SGTA; 2 3 Q9 ZXMS6005SGTA; 2 3 +12V_RAW; 2 R²² 4.7k R²¹ 4.7k Q7 ZXMS6005SGTA 1; 2 Q8 ZXMS6005SGTA

File: LS4.kicad_sch Sheet: /Low Side 2A/ rusefi.com

Id: 4/5 Title: UAEFI Low Side

D Date: 2023-11-01 KiCad; kicad-cli; 7.0.9-7.0.9~ubuntu22.04.1 Size: A4; Rev:; GND; 2 3 Q11 AO3400A GND GND; 3 D6PSM712-LF GND R26 4.7k 12; IN1 OUT1 OUT2; 2 3 GND GND; D6PSM712-LF; 3 D7PSM712-LF; 2 3 GND

3 D7PSM712-LF GND GND R25 4.7k

3 GND GND R25 4.7k R26 4.7k GND Q12 AO3400A

Id: 5/5 Title: UAEF Low Side low current File: LS_weak.kicad_sch Sheet: /Low Side/ rusefi.com


Id: 9/5 Title: UAEFI Injector File: INJ6.kicad_sch Sheet: /Injector/ rusefi.com


Hellen One : Power-Module interface

Reverse polarity and overvoltage protection
F410 V12_RAW


## +5VGND

## +5VGND


Outputs a pulse on rising edge R751

Vref generation RS Latch Tracks which edge happened last
4 GND GND

Differential to single ended conversion

Outputs a pulse on falling edge


Id: 1/1 Title: VR MAX9924 module

+3.3V C616

27k +


100n GND GND R⁶⁰⁸ ⁴⁷

1 PA4 10 PA5 11 PA6 12 PA7 13 PB0 14 PB1 15 VSS 16 VDDIO2 17 PA8 18 PA9 19 PF0 2 PA10 20 PA11 21 PA12 22 PA13 23 PA14 24 PA15 25 PB3 26 PB4 27 PB5 28 PB6 29 PF1 3 PB7 30 PB8 31 VSSA 32 NRST 4 VDDA

1u GND GND GND
+3.3V R⁶¹¹ ²⁰k R⁶¹⁰ ²⁰k GND

to ground to improve the routing
(floating pins by the software).

Heater negative Power GND

VDDA GND
Nernst Sense Voltage Buffer Nernst Internal Resistance Measurement

+3.3V C606 DNP GND
File: hellen1-wbo.kicad_sch Sheet: / rusefi.com V⁻ 11 V⁺

Vdd 4; Vss 6; MCP6004; GNDA; OUT1; OUT2; OUT3; OUT4; C180 PIC18001 100n; PIC18002 COC3; PIR18001; PIR18002; PIR18003; PIR18004; PIR18005; PIR18006; PIR18007; PIR18008; COR5; PIR18101; PIR18102; PIR18103; PIR18105; PIR18104; PIR18106; PIR18107; PIR18108; COR6; PIU18001; PIU18002; PIU18003; PIU18004; PIU18005; PIU18006; PIU18007; PIU18008; PIU18009; PIU180010; PIU180011; PIU180012; PIU180013; PIU180014; COU2; PIC18001; POOUT2; POOUT1; POOUT3; POOUT4; POIN1; POIN3 PIU18005; PIU180010 POIN4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

Vdd 4; Vss 6; MCP6004; GNDA; OUT1; OUT2; OUT3; OUT4; C185 PIC18501 100n; PIC18502 COC3; PIR18501; PIR18502; PIR18503; PIR18504; PIR18505; PIR18506; PIR18507; PIR18508; COR5; PIR18601; PIR18602; PIR18603; PIR18605; PIR18604; PIR18606; PIR18607; PIR18608; COR6; PIU18501; PIU18502; PIU18503; PIU18504; PIU18505; PIU18506; PIU18507; PIU18508; PIU18509; PIU185010; PIU185011; PIU185012; PIU185013; PIU185014; COU2; PIC18501; POOUT2; POOUT1; POOUT3; POOUT4; POIN1; POIN3 PIU18505; PIU185010 POIN4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

Vdd 4; Vss 6; MCP6004; GNDA; OUT1; OUT2; OUT3; OUT4; C190 PIC19001 100n; PIC19002 COC3; PIR19001; PIR19002; PIR19003; PIR19004; PIR19005; PIR19006; PIR19007; PIR19008; COR5; PIR19101; PIR19102; PIR19103; PIR19105; PIR19104; PIR19106; PIR19107; PIR19108; COR6; PIU19001; PIU19002; PIU19003; PIU19004; PIU19005; PIU19006; PIU19007; PIU19008; PIU19009; PIU190010; PIU190011; PIU190012; PIU190013; PIU190014; COU2; PIC19001; POOUT2; POOUT1; POOUT3; POOUT4; POIN1; POIN3 PIU19005; PIU190010 POIN4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

SPI_; VCC; 5 SPI_SCK; 7 SPI_O; lex MicroSD; _MIS


R143 populated: analog input O2S
R145 populated: WAKEUP by CAN

*VIGN input is unprotected!
*A21 is duplicated for ADC and EINT




D100 PESD1CAN; GND; TXD 1 GND 2 VCC 3; Vio; 5 RXD 4; CANL; 6 CANH; TJA1051T/3/1J; CAN_TX; CAN_RX; VCC; CANH; CANL C100 100n
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

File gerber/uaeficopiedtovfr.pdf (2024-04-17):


MAX current 2A E EA MUST USE DUMB COIL SETUP IN IGNITION SHEET!!!!!

CAM+
clutchdiodewiringstufffigurethisoutlater TPS CLT SGND

Analog/digital Heater negative Power GND

enable the CAN WAKEUP
input will be unavailable.

use ADC3 for receiving
the analog signal VR1
instead of the knock
signal

GNDA
VBUS USB- USB+ USB- VBUS USB+ VBUS


File: IGN6.kicad_sch Sheet: /Ignition/ rusefi.com

Id: 2/5 Title: UAEFI Ignition


File: LS4.kicad_sch Sheet: /Low Side 2A/ rusefi.com

Id: 4/5 Title: UAEFI Low Side


3 D6PSM712-LF GND R26 4.7k 470k R16 GND GND

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


Id: 9/5 Title: UAEFI Injector File: INJ6.kicad_sch Sheet: /Injector/ rusefi.com

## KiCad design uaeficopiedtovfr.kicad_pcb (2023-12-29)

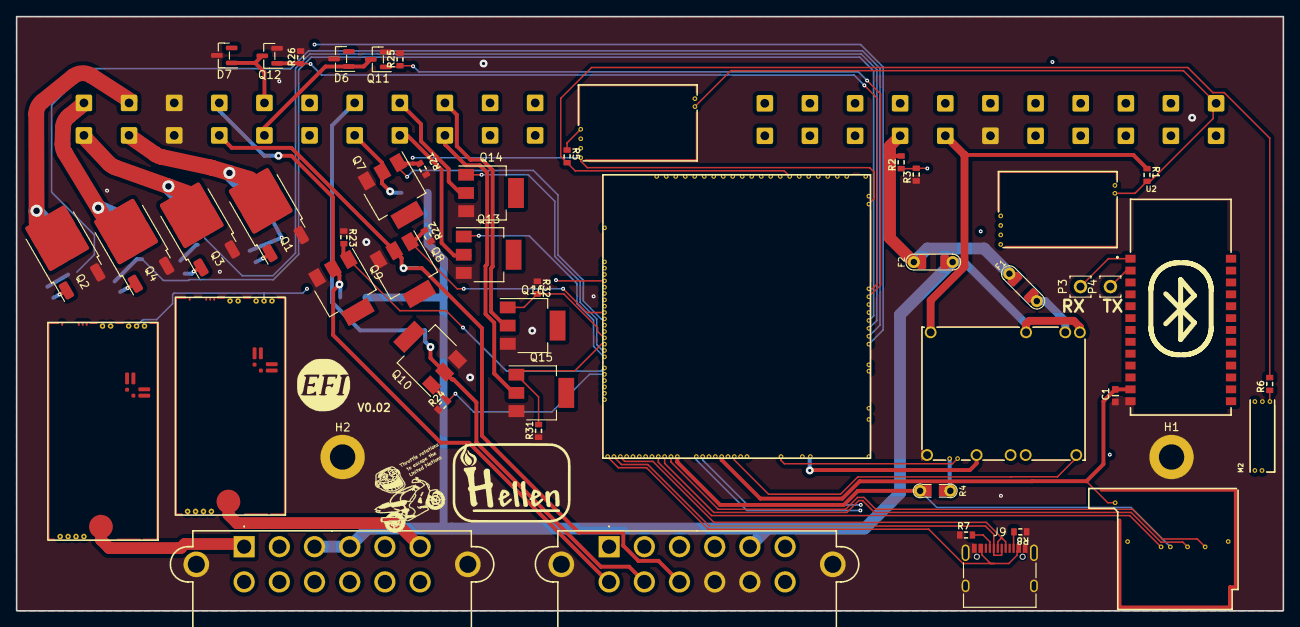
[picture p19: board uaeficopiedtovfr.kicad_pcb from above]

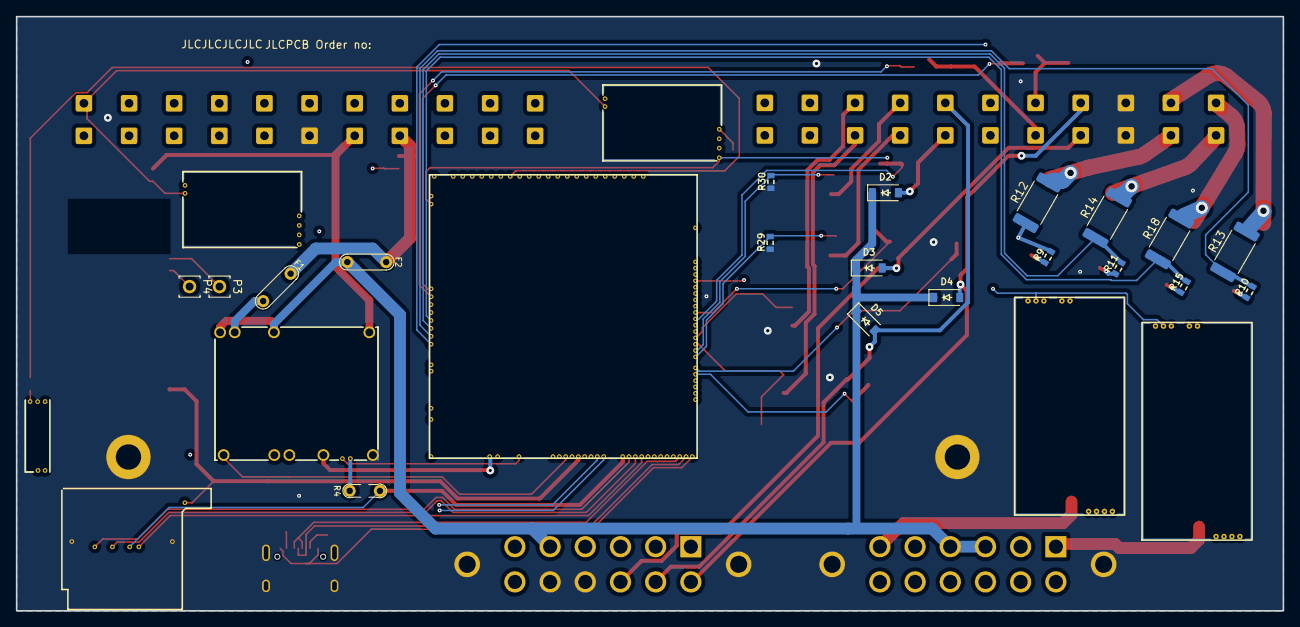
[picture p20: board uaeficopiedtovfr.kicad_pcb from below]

Board: 4 copper layers, 160.0 x 75.0 mm, 69 parts (14 on the bottom side), 89 nets.

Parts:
C1: 100n; C0603
D2, D3, D4, D5: B5819W; SOD-123
D6, D7: PSM712-LF; SOT-23
F1, F2: 12H1500D; PAD-1206-PAD
G3: RUSEFI_LOGO; rusefi_logo
G4: LOGO
H1, H2: MountingHole_Pad; MountingHole_3.2mm_M3_DIN965_Pad
J1, J4: DTF13-12PB; DTF1312PB
J9: USB_C_Receptacle_USB2.0; USB_C_Receptacle_XKB_U262-16XN-4BVC11
M1: Module-power_12and5V-0.2; power_12and5V
M2: Module-knock-0.2; knock
M3: Module-vr-discrete-0.4; vr-discrete
M4: Module-vr-max9924-0.1; vr-max9924
M5, M7: Module-wbo-0.5; wbo
M6: Module:mega-mcu100/0.2; mega-mcu100
M8: Module-sd-0.1; sd
P3, P4: Pad; PAD-TH
Q1, Q2, Q3, Q4: ISL9V3040D3S; TO-252-2
Q7, Q8, Q9, Q10, Q13, Q14, Q15, Q16: ZXMS6005SGTA; SOT-223
Q11, Q12: AO3400A; SOT-23
R1, R21, R22, R23, R24, R25, R26, R29, R30, R31, R32: 4.7k; R0603
R2: 33k; R0603
R3: 6.8k; R0603
R4: Jumper-Pad-Pad; PAD-0805-PAD
R5, R6: 0; R0603
R7, R8: 5.6k; R0603
R9, R10, R11, R15: 22; R0603
R12, R13, R14, R18: 0; R_2512_6332Metric
U1: VFRboardempty
U2: JDY-33
text1: trollfaceVFR

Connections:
+3.3VA: C1.2, M6.N15 (V33_SWITCHABLE), M8.V1 (V33), U2.12 (3V3)
+5V: M1.E4 (V5), M6.N22 (VCC)
+5VA: M2.E1 (V5A), M3.E4 (V5_IN), M4.E4 (V5_IN), M5.W1 (V5_IN), M6.E1 (V5A_SWITCHABLE), M6.W2 (V5A_SWITCHABLE), M7.W1 (V5_IN)
+5VP: M1.V4 (5VP), R1.1, U1.B7
+12V: F1.1, F2.1, R2.2, U1.B8
+12V_RAW: D2.1 (K), D3.1 (K), D4.1 (K), D5.1 (K), F2.2, J1.3, J1.4, J4.5, M1.V1 (V12_PERM), M1.V3 (V12_RAW)
/ADC3: M6.S15 (IN_KNOCK_(PA2)), R5.2, R6.2
/BARO: M6.S7 (IN_AUX3_(PC5)), U1.B4
/CAM+: M3.W2 (VR+), U1.B11
/CAM/CRANK-: M3.W1 (VR-), M4.W1 (VR-), R1.2, U1.B12
/CAN+: J4.7, M5.W4 (CANH), M6.W11 (CANH), M7.W4 (CANH)
/CAN-: J4.6, M5.W3 (CANL), M6.W12 (CANL), M7.W3 (CANL)
/CLT: M6.S21 (IN_CLT_(PC2)), U1.B15
/CRANK+: M4.W2 (VR+), U1.B22
/FILIGHT: D6.1, Q11.2 (D), U1.A7
/FUELPUMP_LS: D2.2 (A), Q7.2 (D), U1.A5
/IAT_SENSOR: M6.S20 (IN_IAT_(PC3)), U1.B5
/IGN1: M6.W10 (IGN1_(PC13)), R9.2, R12.1
/IGN2: M6.W9 (IGN2_(PE5)), R10.2, R13.1
/IGN3: M6.W8 (IGN3_(PE4)), R11.2, R14.1
/IGN4: M6.W7 (IGN4_(PE3)), R15.2, R18.1
/IGNOUT1: Q1.2 (C), R12.2, U1.A10
/IGNOUT2: Q2.2 (C), R13.2, U1.A21
/IGNOUT3: Q3.2 (C), R14.2, U1.A11
/IGNOUT4: Q4.2 (C), R18.2, U1.A22
/INJ1: M6.E17 (OUT_INJ1_(PD3)), Q13.1 (G), R29.2
/INJ2: M6.E16 (OUT_INJ2_(PA9)), Q14.1 (G), R30.2
/INJ3: M6.E15 (OUT_INJ3_(PD11)), Q15.1 (G), R31.2
/INJ4: M6.E14 (OUT_INJ4_(PD10)), Q16.1 (G), R32.2
/INJOUT1: Q13.2 (D), U1.A4
/INJOUT2: Q14.2 (D), U1.A15
/INJOUT3: Q15.2 (D), U1.A3
/INJOUT4: Q16.2 (D), U1.A14
/INTAKEFLAP: D5.2 (A), J4.11, Q10.2 (D), U1.A16
/IN_FLEX: J4.3, M6.S17 (IN_VSS_(PE11))
/IN_HALL1: M6.S4 (IN_D1_(PE12)), U1.B17
/IN_KNOCK: M2.E3 (OUT_KNOCK), R6.1
/IN_KNOCK_RAW: J4.4, M2.W1 (IN_KNOCK)
/IN_MAP: M6.S13 (IN_MAP1_(PC0)), U1.B3
/IN_TPS1: M6.S18 (IN_TPS_(PA4)), U1.B14
/IN_VIGN: F1.2, M1.V2 (IN_VIGN)
/IN_VMAIN: M6.S6 (IN_AUX4_(PA7)), R2.1, R3.2
/LS1: M6.E11 (OUT_INJ7_(PD15)), Q7.1 (G), R21.2
/LS2: M6.E10 (OUT_INJ8_(PD12)), Q8.1 (G), R22.2
/LS3: M6.E18 (OUT_PWM1_(PD13)), Q9.1 (G), R23.2
/LS4: M6.E19 (OUT_PWM2_(PC6)), Q10.1 (G), R24.2
/LS_WEAK1: M6.W4 (IGN7_(PB9)), Q11.1 (G), R25.1
/LS_WEAK2: M6.W3 (IGN8_(PE6)), Q12.1 (G), R26.1
/OUT_LS2: D3.2 (A), J4.10, Q8.2 (D), U1.A8
/OUT_LS3: D4.2 (A), J4.12, Q9.2 (D), U1.A19
/OUT_LS_WEAK2: D7.1, Q12.2 (D), U1.A18
/PG_5VP: M6.N12 (SPI3_MOSI_(PC12)), M8.V5 (SD_MOSI), R4.2
/PWR_EN: M1.E5 (EN_5VP), M6.N20 (OUT_PWR_EN_(PE10))
/USB+: J9.A6 (D+), J9.B6 (D+), M6.N3 (USBP_(PA12))
/USB-: J9.A7 (D-), J9.B7 (D-), M6.N2 (USBM_(PA11))
/VBAT: M1.E1 (VBAT), M6.N17 (VBAT)
/VBUS: J9.A4 (VBUS), J9.A9 (VBUS), J9.B4 (VBUS), J9.B9 (VBUS), M6.N1 (VBUS)
/VIGN: M1.E3 (VIGN), M6.E5 (IN_VIGN_(PA5))
/VR1: M3.E3 (OUT), M6.N18 (UART8_RX_(PE0))
/VR1_A: M3.E2 (OUT_A), R5.1
/VR1_THRESHOLD: M3.E1 (Thresh_IN), M6.E23 (OUT_PWM6_(PD14))
/VR2: M4.E3 (OUT), M6.N19 (UART8_TX_(PE1))
/VREF1: M2.W2 (VREF), M6.S22 (VREF1)
/WBO2_Heater: J1.1, M7.E5 (LSU_H+)
/WBO2_Ip: J1.11, M7.E3 (LSU_Ip)
/WBO2_Rtrim: J1.2, M7.E4 (LSU_Rtrim)
/WBO2_Un: J1.10, M7.E1 (LSU_Un)
/WBO2_Vm: J1.12, M7.E2 (LSU_Vm)
/WBO_Heater: J1.6, M5.E5 (LSU_H+)
/WBO_Ip: J1.8, M5.E3 (LSU_Ip)
/WBO_Rtrim: J1.5, M5.E4 (LSU_Rtrim)
/WBO_Un: J1.9, M5.E1 (LSU_Un)
/WBO_Vm: J1.7, M5.E2 (LSU_Vm)
GND: C1.1, D6.2, D7.2, H1.1, H2.1, J1.MH1, J1.MH2, J4.8, J4.9, J4.MH1, J4.MH2, J9.A1 (GND), J9.A12 (GND), J9.B1 (GND), J9.B12 (GND), J9.S1 (SHIELD), M1.S1 (GND), M2.E2 (GND), M3.G (GND), M4.G (GND), M5.E6 (LSU_H-), M5.G (GND), M6.G (GND), M7.E6 (LSU_H-), M7.G (GND), M8.G (GND), M8.V2 (GND), M8.V3 (GND), Q1.3 (E), Q2.3 (E), Q3.3 (E), Q4.3 (E), Q7.3 (S), Q8.3 (S), Q9.3 (S), Q10.3 (S), Q11.3 (S), Q12.3 (S), Q13.3 (S), Q14.3 (S), Q15.3 (S), Q16.3 (S), R3.1, R7.1, R8.1, R21.1, R22.1, R23.1, R24.1, R25.2, R26.2, R29.1, R30.1, R31.1, R32.1, U1.A9, U1.A20, U1.B6, U2.13 (GND)
GNDA: M6.W1 (GNDA), U1.B2
unnamed: J9.A5 (CC1), R7.2
unnamed: J9.B5 (CC2), R8.2
unnamed: M1.E6 (PG_5VP), R4.1
unnamed: M5.J1 (SEL1), M5.J_GND1 (PULL_DOWN1)
unnamed: M6.N9 (SPI3_CS_(PA15)), M8.V4 (SD_CS)
unnamed: M6.N11 (SPI3_MISO_(PC11)), M8.V7 (SD_MISO)
unnamed: M6.N10 (SPI3_SCK_(PC10)), M8.V6 (SD_SCK)
unnamed: M6.N14 (UART2_RX_(PD6)), P3.1, U2.1 (TXD)
unnamed: M6.N13 (UART2_TX_(PD5)), P4.1, U2.2 (RXD)
unnamed: M7.J1 (SEL1), M7.J_GND1 (PULL_DOWN1)
unnamed: Q1.1 (G), R9.1
unnamed: Q2.1 (G), R10.1
unnamed: Q3.1 (G), R11.1
unnamed: Q4.1 (G), R15.1

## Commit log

2023-12-28 renamed board to uaEFIVFR so the script runs
    [uaEFIVFR.kicad_pcb]
2023-12-28 copied project folder over to git folder
    I am not good with computer
    [CAN.kicad_sch, DC_MOTOR_0.1.kicad_sch, IGN6.kicad_sch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]
2023-12-28 Added origin for drill file
    [uaEFIVFR.kicad_pcb, uaeficopiedtovfr.kicad_pcb]
2023-12-28 [skip actions] Auto-generated board
    [uaeficopiedtovfr-B_Cu.gbl, uaeficopiedtovfr-B_Mask.gbs, uaeficopiedtovfr-B_Paste.gbp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]
2023-12-28 deleted junk files
    [CAN.kicad_sch, INPUTS.kicad_sch, MCU.kicad_sch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]
2023-12-28 changed BOM filename
    [bom_replace_uaeficopiedtovfr-0.00.csv]
2023-12-28 Re-added graphics to board
    [uaeficopiedtovfr.kicad_pcb]
2023-12-28 removed old gerbers
    [uaeficopiedtovfr-B_Cu.gbl, uaeficopiedtovfr-B_Mask.gbs, uaeficopiedtovfr-B_Paste.gbp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]
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2023-12-28 i am not gud with computer
    [uaeficopiedtovfr-B_Cu.gbl, uaeficopiedtovfr-B_Mask.gbs, uaeficopiedtovfr-B_Paste.gbp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]
2023-12-28 added ref to graphics
    [uaeficopiedtovfr.kicad_pcb, uaeficopiedtovfr.kicad_sch]
2023-12-28 Changed drill origin
    Previous file had all the modules offset vertically, moved the drill location from the corner of the board to below the deutsch connectors to see if that fixed it
    [uaeficopiedtovfr-0.00-BOM-JLC.csv, uaeficopiedtovfr-0.00-BOM.csv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]
2023-12-28 Moved drill file again
    last commit offset it 25mm in the opposite direction
    [uaeficopiedtovfr-0.00-BOM-JLC.csv, uaeficopiedtovfr-0.00-BOM.csv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]
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2023-12-28 generate 4 layer board
    [CAN.kicad_sch, INPUTS.kicad_sch, MCU.kicad_sch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]
2023-12-28 Added SD card support, cleaned up ignition traces
    [uaeficopiedtovfr-0.01-BOM-JLC.csv, uaeficopiedtovfr-0.01-BOM.csv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]
2023-12-28 forgot to increment the BOM yet again
    [bom_replace_uaeficopiedtovfr-0.02.csv]
2023-12-28 adding jlcpcb order number to silkscreen
    [uaeficopiedtovfr-0.02-BOM-JLC.csv, uaeficopiedtovfr-0.02-BOM.csv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]
2023-12-29 removed DNP from ignition drivers
    [IGN6.kicad_sch, uaeficopiedtovfr.kicad_pcb]
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2023-12-29 board still isn't exporting with ignition drivers for some reason
    [uaeficopiedtovfr-0.02-BOM-JLC.csv, uaeficopiedtovfr-0.02-BOM.csv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]
2023-12-29 Added board art
    I hate the antichrist
    [uaeficopiedtovfr-0.02-BOM-JLC.csv]
2023-12-29 Removed board art
    filling the entire backside with 0.4mm tall text made the gerbers over 100MB
    [uaeficopiedtovfr-0.02-BOM-JLC.csv, uaeficopiedtovfr-0.02-BOM.csv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]
2023-12-30 Fixed error on connector pinout
    [uaeficopiedtovfr-0.02-BOM-JLC.csv, uaeficopiedtovfr-0.02-BOM.csv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]
2023-12-30 Routed B10 and B21 to button inputs 1 and 2
    These have something to do with killing the engine if you put it in gear with the kickstand down or try to start it in gear with the kickstand down
    [uaeficopiedtovfr-0.02-BOM-JLC.csv, uaeficopiedtovfr-0.02-BOM.csv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]
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2023-12-31 Changed two deutsch connectors to single ampseal
    I did some fitment tests and decided a single big connector dead center in the board will fit the best
    [bom_replace_uaeficopiedtovfr-0.02.csv, bom_replace_uaeficopiedtovfr-0.03.csv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]
2023-12-31 Changed rear connector to single ampseal
    I did some fitment tests on my bike and a single rear connector in the center of the board will be far easier to fit
    [uaeficopiedtovfr-0.03-BOM-JLC.csv, uaeficopiedtovfr-0.03-BOM.csv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]
2023-12-31 Moved drill file
    board is generating with offset modules again
    [uaeficopiedtovfr-0.03-BOM-JLC.csv, uaeficopiedtovfr-0.03-BOM.csv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]
2023-12-31 Moved drill again
    Offset still exists
    [uaeficopiedtovfr-0.03-BOM-JLC.csv, uaeficopiedtovfr-0.03-BOM.csv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]
2023-12-31 Added art to board, updated README
    Included other potential ECU applications in readme and added some ♂art♂ to the front silkscreen
    [uaeficopiedtovfr-0.03-BOM-JLC.csv, uaeficopiedtovfr-0.03-BOM.csv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]
2023-12-31 Added indicator for drill origin
    there was still an offset lol
    [uaeficopiedtovfr-0.03-BOM-JLC.csv, uaeficopiedtovfr-0.03-BOM.csv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]
2023-12-31 THERE'S STILL AN OFFSET
    Moved drill origin to left corner of main board area, if it's in line with the protrusion for the rear connector all hellen modules end up with an offset equal to 5mm or however far that sticks out
    [uaeficopiedtovfr-0.03-BOM-JLC.csv, uaeficopiedtovfr-0.03-BOM.csv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]
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2023-12-31 forgot to clear old gerbers
    [uaeficopiedtovfr-0.03-BOM-JLC.csv, uaeficopiedtovfr-0.03-BOM.csv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]
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2023-12-31 Drill origin getting closer
    dfisudhfuishdfuishdf
    [uaeficopiedtovfr-0.03-BOM-JLC.csv, uaeficopiedtovfr-0.03-BOM.csv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]
2023-12-31 Drill origin
    X is aligned now this should align Y
    [uaeficopiedtovfr-0.03-BOM-JLC.csv, uaeficopiedtovfr-0.03-BOM.csv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]
2024-01-01 Removed redundant SD card, moved rear connector inwards
    [uaeficopiedtovfr-0.03-BOM-JLC.csv, uaeficopiedtovfr-0.03-BOM.csv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]
2024-01-02 Beefed up 12V rail
    [uaeficopiedtovfr-0.03-BOM-JLC.csv, uaeficopiedtovfr-0.03-BOM.csv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]
2024-01-02 Routed aux2 and button3 to rear connector
    Routed aux2 and button3 to rear connector
    [uaeficopiedtovfr-0.03-BOM-JLC.csv, uaeficopiedtovfr-0.03-BOM.csv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]
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2024-01-05 swapped left and right connectors
    Had the wrong idea about what was the A vs B connector, board needs routing finished
    [uaeficopiedtovfr.kicad_sch]
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2024-01-05 Fixed routing
    Moved trace that was routed through the MCU footprint
2024-01-06 Revert "Merge branch 'master' of https://github.com/VFRenjoyer/hellen-VFR800"
    This reverts commit 55b484720920c2f59454420a7e030c13d3190a57, reversing
    changes made to 5f9ad006efecef1979d649e5e48fa4e9a59aecf5.
    [bom_replace_uaeficopiedtovfr-0.03.csv, uaeficopiedtovfr-0.03-BOM-JLC.csv, uaeficopiedtovfr-0.03-BOM.csv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]
2024-01-08 Routed AUX1 input to back connector
    RIP knock sensor option
    [uaeficopiedtovfr.kicad_sch]
2024-01-19 Corrected 12V not being connected to A5, removed unused lowside driver
2024-01-20 Revert "Corrected 12V not being connected to A5, removed unused lowside driver"
    This reverts commit b6bd63c4784d258af73e442f4c1ae07db6db8b04.
2024-02-11 Added jumpers for power to BT module and both WBO modules
    [uaeficopiedtovfr.kicad_sch]
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2024-02-13 fixed rear connector position, made USB more practical
    Rounded off corners, changed USB connector, moved AMPSeal connector closer to board edge, changed some routing
    [uaeficopiedtovfr.kicad_sch]
2024-02-13 Silkscreen fix
    Fixed R2 floating in space
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2024-02-17 Moved some traces
    clearance paranoia
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2024-04-11 0.04 revB begins
    Added pullup resistor so tach works
    [IGN6.kicad_sch, INJ6.kicad_sch, LS4.kicad_sch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]
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2024-04-14 scripts couldn't find schematic?
    [uaeficopiedtovfr.kicad_sch]
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2024-04-17 [skip actions] Auto-generated board v2.1
    [uaeficopiedtovfr-B_Cu.gbl, uaeficopiedtovfr-B_Mask.gbs, uaeficopiedtovfr-B_Paste.gbp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]
